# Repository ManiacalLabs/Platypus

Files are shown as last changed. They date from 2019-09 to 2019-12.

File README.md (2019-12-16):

# Platypus CNC / Laser Control Board

The Platypus is an Open Hardware CNC / Laser control board for running 2-axis GRBL with a wide variety of stepper motor driver options.

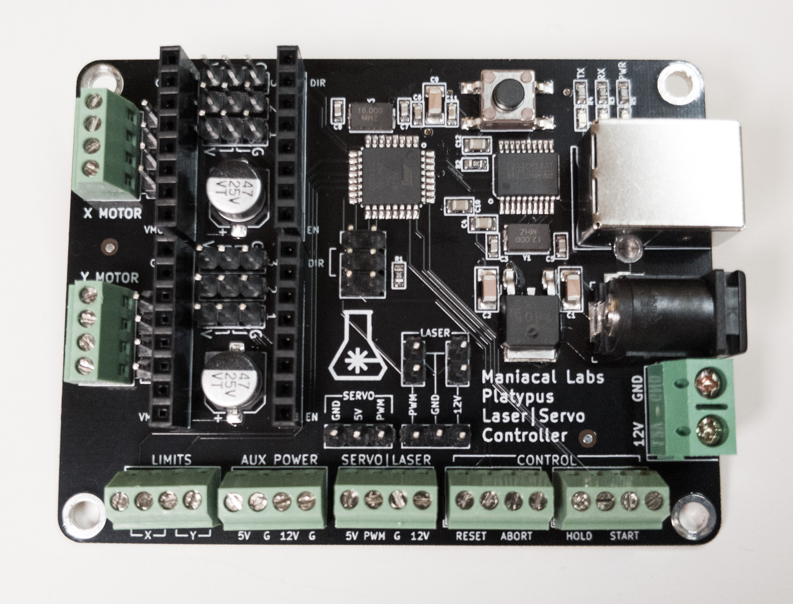
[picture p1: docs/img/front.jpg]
Platypus Controller Board


Unlike other Grbl boards that are just Arduino shields, the Platypus is a fully integrated solution with a built-in ATMega328p microcontroller and USB UART. 

Also, while other Grbl boards ignore it, the Platypus natively supports configuring Trinamic (TMC) StepStick drivers like the TMC2100 and TMC2208. Unlike normal StepStick motor drivers, the TMC variants use tri-state config pins which the Platypus provides.

# Specs

- Integrated ATMega328p Microcontroller (no arduino needed)
- CH340 USB to UART converter
- Screw terminals for all connections (plus male headers for motor and laser)
- Supports all standard StepStick-style motor drivers including TMC2100 and TMC2208
- Only 57mm x 75mm
- Robust USB-B connector

# Important Links

- [Usage](docs/Usage.md)
- [Assembly](docs/Assembly.md)

# Dimensions

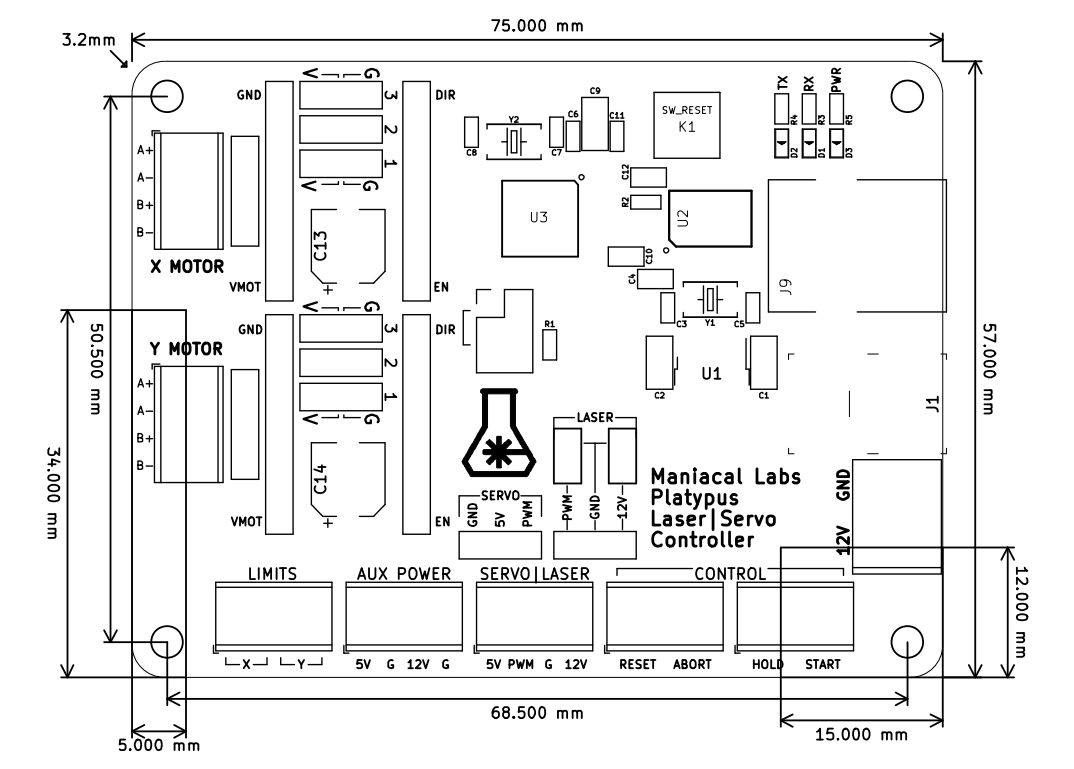
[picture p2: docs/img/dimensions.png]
Dimensions


# Contributing

This repository makes use of `git` submodules (primarily to handle KiCAD symbol and footprint libraries) and must be cloned with extra options.

Either clone the repo via:

```
git clone --recurse-submodules git@github.com:ManiacalLabs/Platypus.git
```

Or, if you already have the repo cloned or are using a fork:

```
git clone <EngravinatorRepo>
cd Engravinator
git submodule init
git submodule update
```

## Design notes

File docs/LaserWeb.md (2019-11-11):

# LaserWeb Software Setup

For using the Platypus with [LaserWeb](https://github.com/LaserWeb/LaserWeb4/) we recommend starting with the official [LaserWeb Machine Profile](https://github.com/LaserWeb/LaserWeb4/wiki/3-Settings-Machine-Profile) documentation.

Open LaserWeb and go to the `Settings` tab, where you can create a new machine profile. Select `Generic GRBL machine` from the drop-down and then click `Apply` to load that base profile.

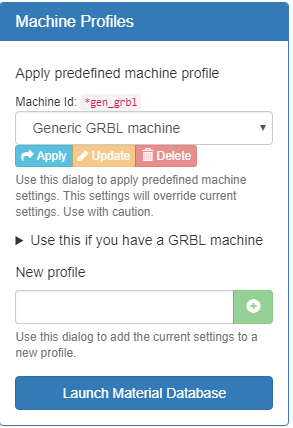
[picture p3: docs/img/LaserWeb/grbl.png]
New machine profile


Now, under the `Machine` section, enter your machine width and height (130x130mm if using the Engravinator). 

If using the Engravinator, in the `Machine Bottom Y` you must enter `-130`. There is a bug in the current UI so it sadly cannot be seen in the screenshot. This offset will be explained below.

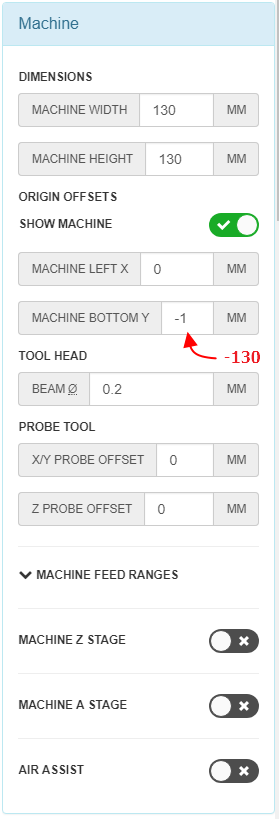
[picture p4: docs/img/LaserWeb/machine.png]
Machine section


The `File Settings` and `GCode` sections require no changes.

Under the `Application` section ensure that your machine height and width are the same values used in the `Machine` section. All other settings should be as shown, especially for the Engravinator.

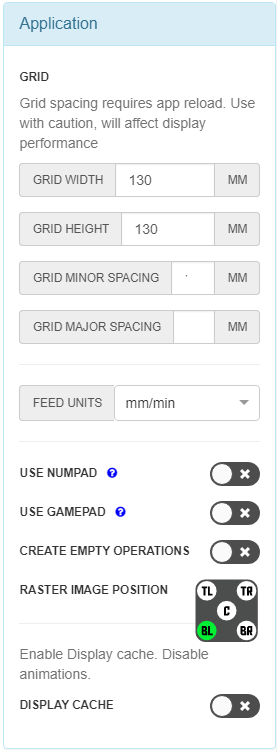
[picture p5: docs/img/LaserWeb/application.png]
Application section


For the Engravinator, you need to set a workspace offset because it does not home to the origin. In the LaserWeb console, enter `G10 L2 P1 X0 Y-130` and press enter. The Platypus comes with this offset preset but it doesn't hurt to enter it again, in case the setting was wiped. It will retain even after a power cycle. This tells the controller that the location it homed to is actually `0,130` instead of `0,0`.

Your workspace should now look as below:

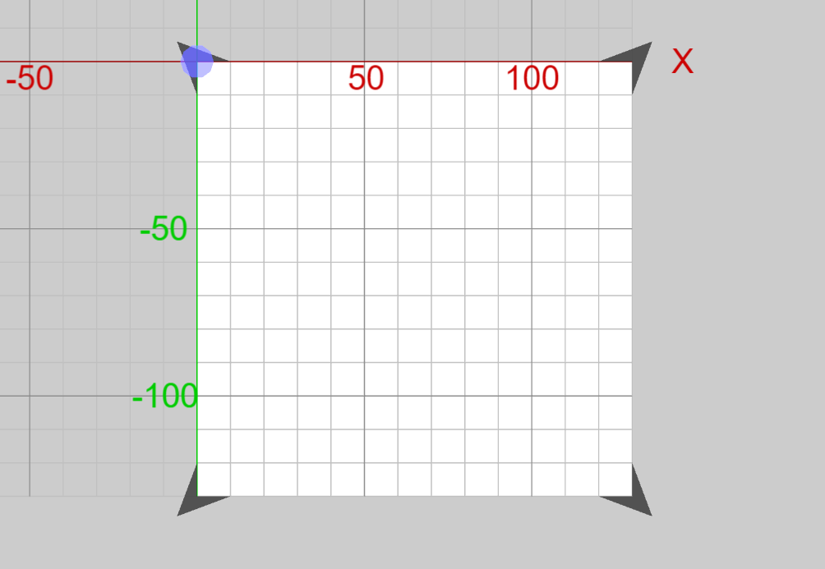
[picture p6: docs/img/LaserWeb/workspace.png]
workspace view


For the Engravinator note that the laser position is marked in the rear-left (or top-left if you prefer). As this is where it homes to, this will be the position seen after homing.

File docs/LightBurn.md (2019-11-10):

# LightBurn Software Setup

For using the Platypus with [LightBurn](https://lightburnsoftware.com) we recommend starting with the official [LightBurn New Device](https://github.com/LightBurnSoftware/Documentation/blob/master/DeviceWizard.md) documentation.

But you can also use the following for a basic setup. Click on the `Devices` button in the `Laser` window.

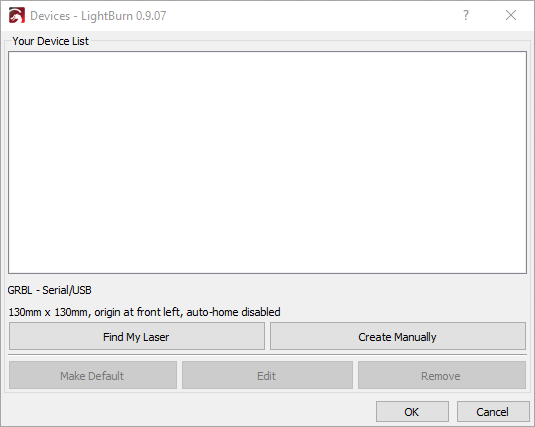
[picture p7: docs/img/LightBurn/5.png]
Devices


Either use `Find My Laser` to automatically detect and add the Platypus or click on `Create Manually`.

If using the manual setup, ensure that you select `GRBL` for the device type dialog:

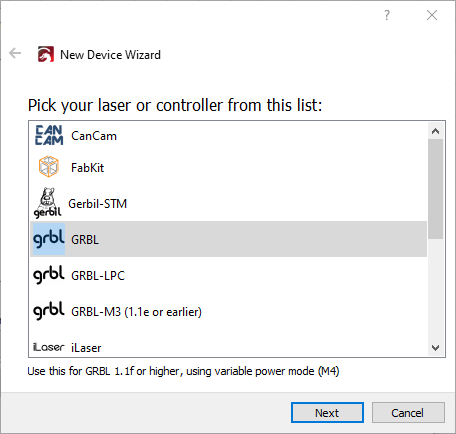
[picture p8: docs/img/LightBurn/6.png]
Device Type


Give the device a name and set your X and Y axis length. In the case of the [Engravinator](https://engravinator.com) both axis should be 130mm.

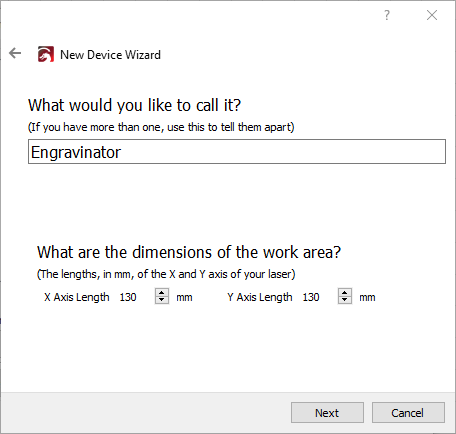
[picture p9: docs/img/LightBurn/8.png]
Name and Size


Set your origin and auto-homing. In the case of the [Engravinator](https://engravinator.com) the origin is **Front Left** even though it homes to **Rear Left**.

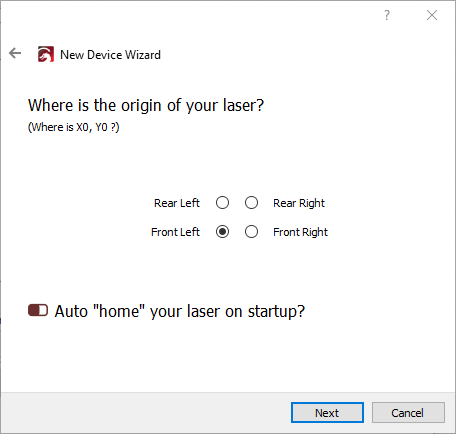
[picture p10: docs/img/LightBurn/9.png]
Origin and Homing


You should now see it connect to the Platypus in the `Console` tab. If it does not, you may need to select the serial port in the drop-down under the `Laser` tab.

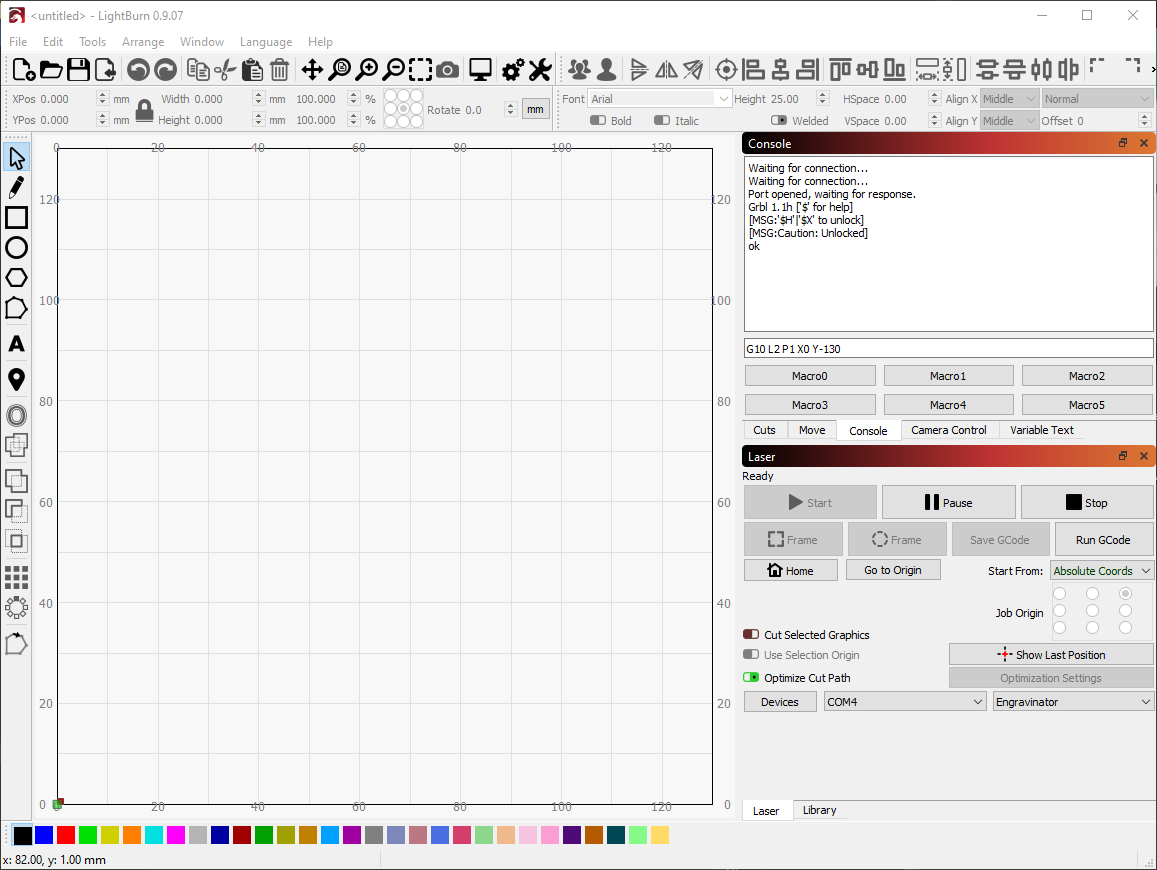
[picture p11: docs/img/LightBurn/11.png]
Connection


Please note that with the [Engravinator](https://engravinator.com) you may need to tell it that the homing location is offset from the origin. In the console, simply enter `G10 L2 P1 X0 Y-130` and press enter. The Platypus comes with this offset preset but it doesn't hurt to enter it again, in case the setting was wiped. It will retain even after a power cycle. This tells the controller that the location it homed to is actually `0,130` instead of `0,0`.

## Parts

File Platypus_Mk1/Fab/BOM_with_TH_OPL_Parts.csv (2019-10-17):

Part/Designator | Manufacture Part Number/Seeed SKU | Quantity
R3,R4,R5 | 301010298 | 3
R1,R2 | 301010299 | 2
C6,C11 | 302010139 | 2
C3,C5,C7,C8 | 302010143 | 4
C4,C10,C12 | 302010165 | 3
C1,C2,C9 | 302010181 | 3
C13,C14 | 302030059 | 2
D1,D2,D3 | 304090042 | 3
Y1 | 306010047 | 1
Y2 | 306010054 | 1
U3 | 310010049 | 1
U2 | 310070026 | 1
K1 | 311020004 | 1
J4,J5 | 320020016 | 2
J12,J14 | 320020017 | 2
J10 | 320020077 | 1
CN1,CN2,CN3,CN4,CN7,CN8,CN9,CN12 | 320020079 | 8
CN5,CN6,CN10,CN11 | 320030061 | 4
J15 | 320110031 | 1
J2,J3,J6,J7,J8,J11,J13 | 320110118 - GS019 4 pin screw terminal | 7
U1 | CJ7805(TO-252-2) 3% | 1

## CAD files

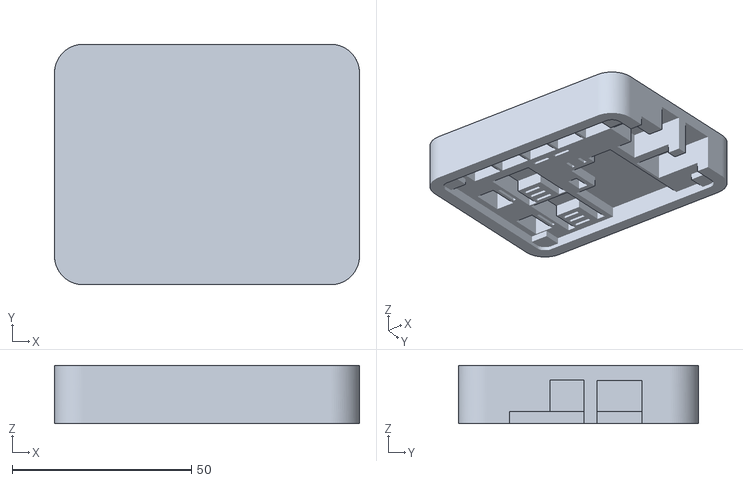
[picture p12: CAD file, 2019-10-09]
Platypus_Mk1/SolderJig.stl
85.0 x 67.0 x 16.2

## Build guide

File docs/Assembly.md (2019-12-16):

# Platypus Assembly

**If you purchased one of the pre-assembled units, you can just skip this guide!**

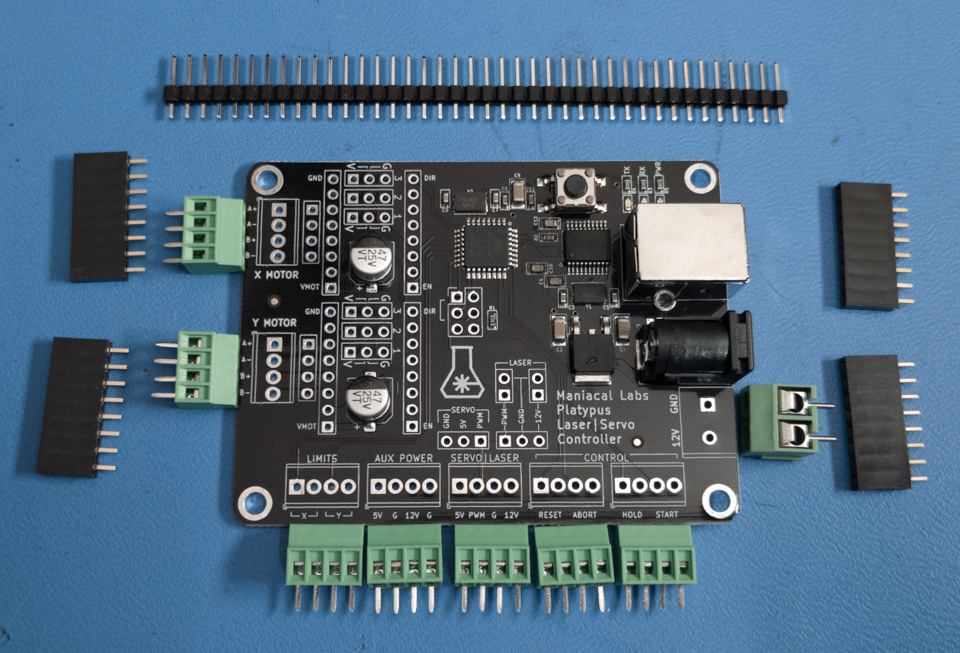
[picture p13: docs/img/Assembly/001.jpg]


Welcome to the wonderful world of the Platypus 2-Axis Laser/Servo controller! We'll be walking you through the assembly of the through-hole components which should only take 10-20 minutes.

First step is to ensure you have all the components shown above. You should have:

- Platypus main PCB
- 7x 4-pin 0.1" screw terminals
- 1x 2-pin 0.2" screw terminal
- 4x 8-pin female header
- 1x 40-pin cuttable male header

Please note that the USB port and power input barrel jack will come pre-assembled (we use these for programming).

Let's get going. We're going to do all components of each type before moving on from shortest to tallest. This allows flipping the board and having those components pushed up against the PCB.

**Note:** *Basically all of these components, except the motor driver headers, are optional depending on what you need. Check out the [Usage](Usage.md) doc and, if you decide you don't need a particular component, feel free to just leave it out.*

## Male Headers

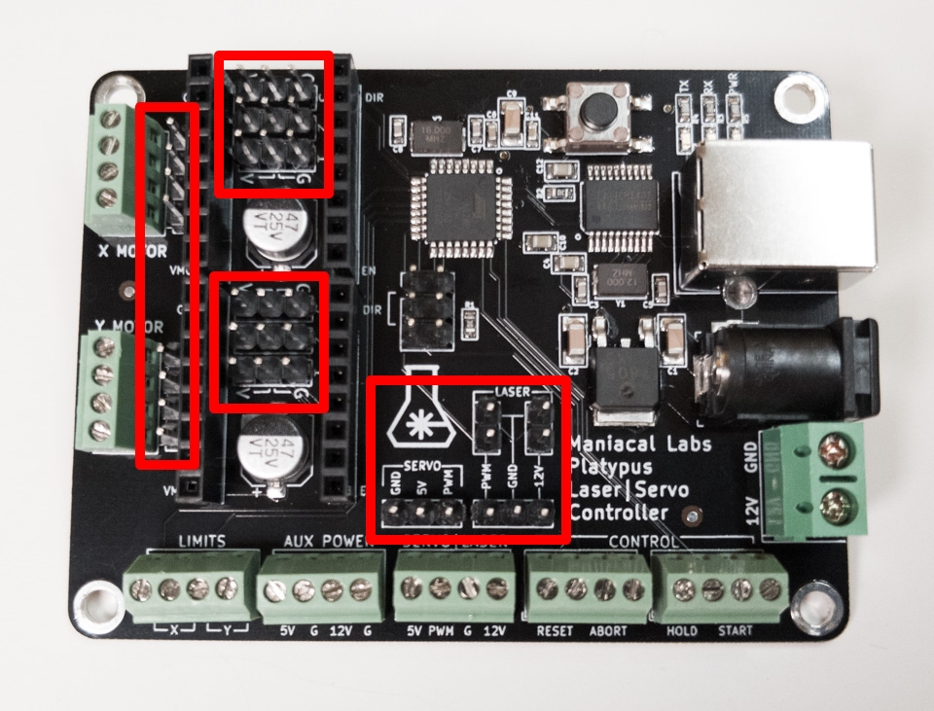
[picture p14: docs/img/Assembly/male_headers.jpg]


**Note:** *The 2x3 pin male header in the middle of the board is not included and will remain unpopulated. This is an ICSP header for programming.*

Use some flush-cut wire snips to break the 40-pin male header into the following sizes:

- 2x 4-pin
- 8x 3-pin
- 2x 2-pin

You will have one 4-pin section left. That's just spare.

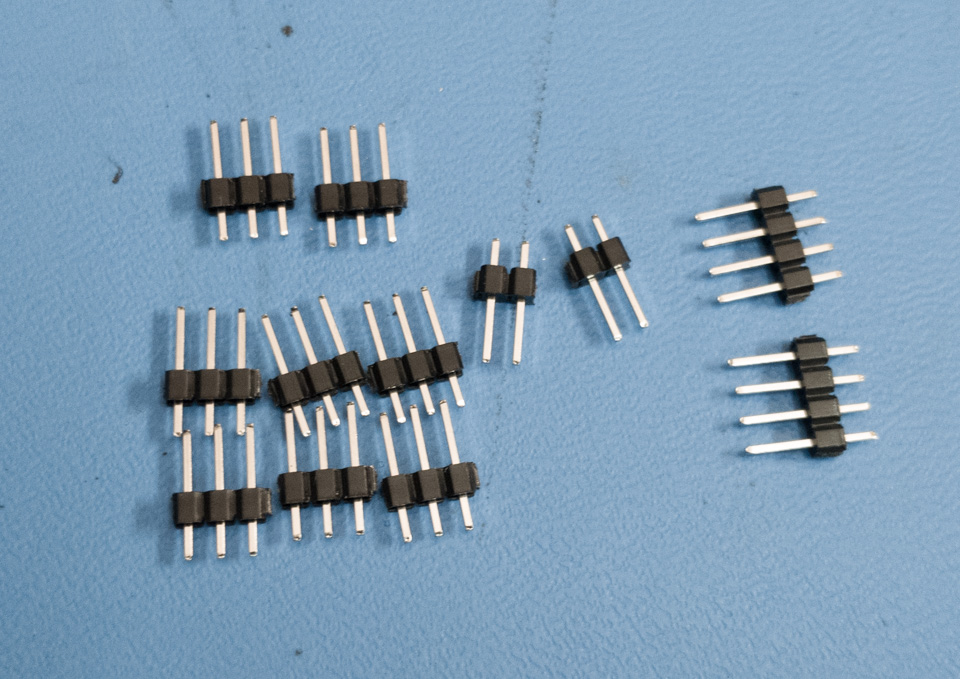
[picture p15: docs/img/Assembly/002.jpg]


For each of the male header sections, insert them into the appropriately sized spot and use some tape to hold them in place, then flip the board.

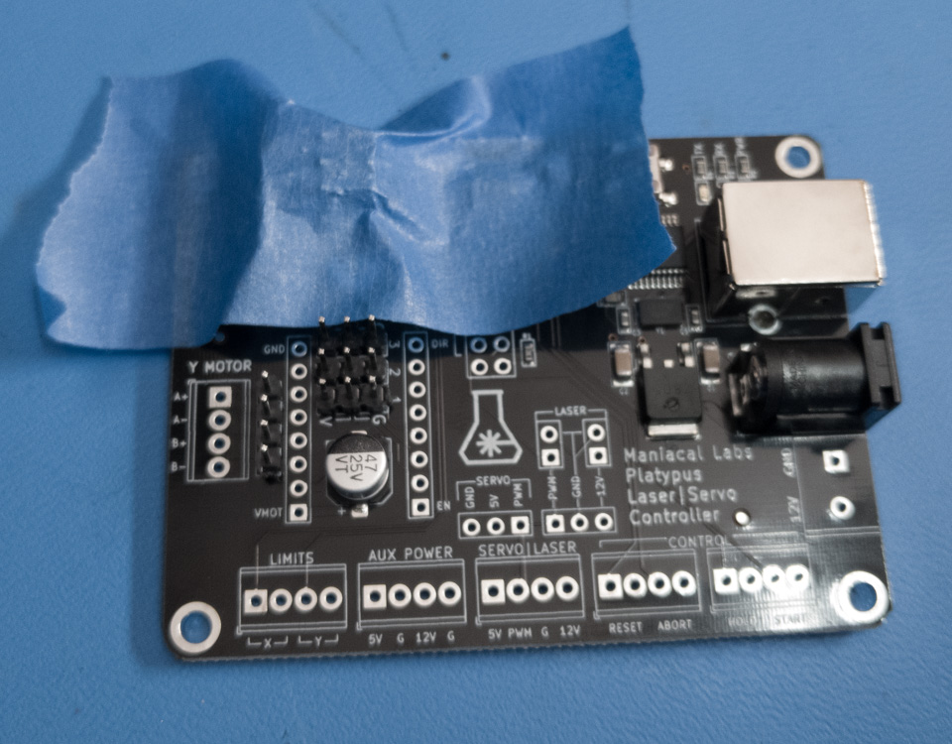
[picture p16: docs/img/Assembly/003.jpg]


**IMPORTANT** *Only solder one pin from each header section at this point!* As shown below.

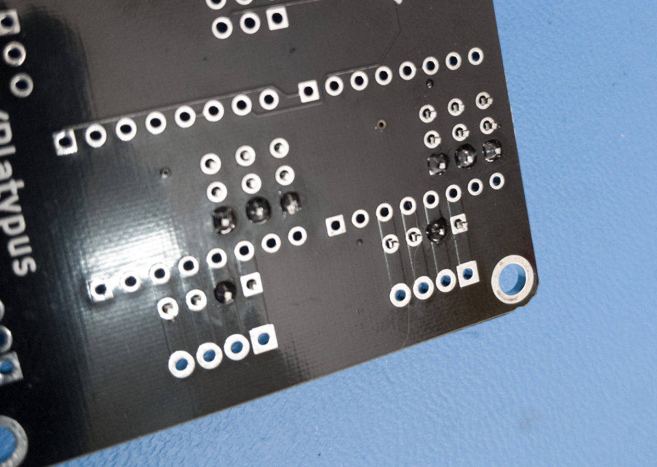
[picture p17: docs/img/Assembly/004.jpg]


Flip the board and remove the tape. If the header does not lie flush and perpendicular to the board, press on one of the pins you **DID NOT** solder with a finger and flip the board back over. Apply heat to the pin you did solder and use your finger to realign the header while the solder is molten.

Once you are happy with all the male headers, flip the board and solder all remaining pins.

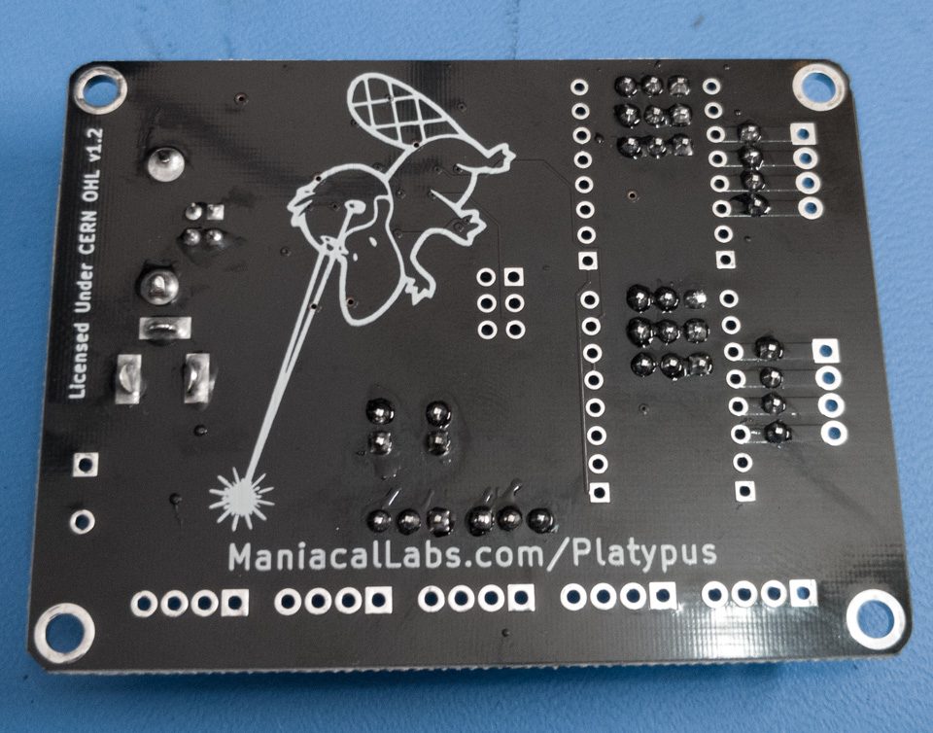
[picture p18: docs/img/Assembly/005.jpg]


## Female Motor Driver Headers

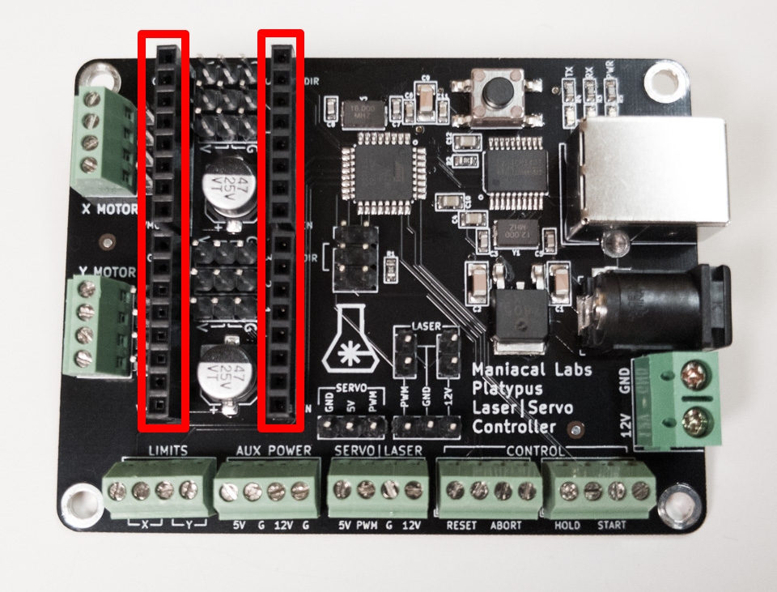
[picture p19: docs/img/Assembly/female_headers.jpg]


For this part it is important that the four 8-pin female headers be aligned correctly. We highly recommend using the (already soldered) motor drivers you plan to use to do this. 

Attach the female headers to the male headers on the motor drivers and then insert the female header pins into the front of the Platypus PCB.

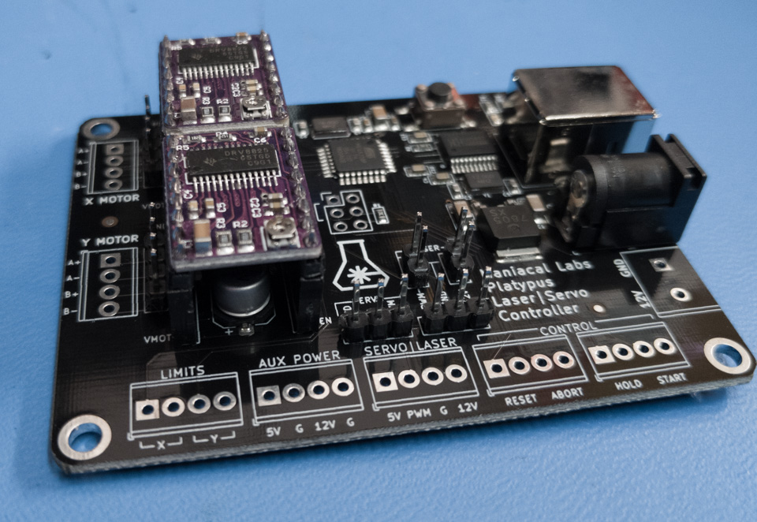
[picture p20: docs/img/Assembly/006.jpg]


Flip the board and solder only 2 pins from each motor driver, on opposing corners, as shown below.

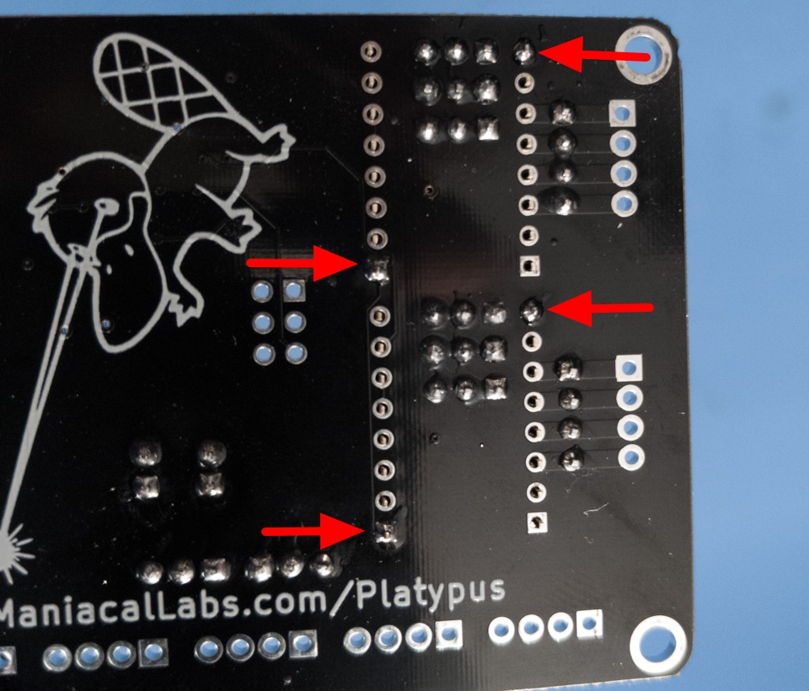
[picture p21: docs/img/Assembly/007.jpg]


Now flip the board back over and ensure that the female headers are sitting flush and perpendicular. If not, heat up the solder on those single pins and adjust. Once everything looks good, flip back over and solder all remaining pins.

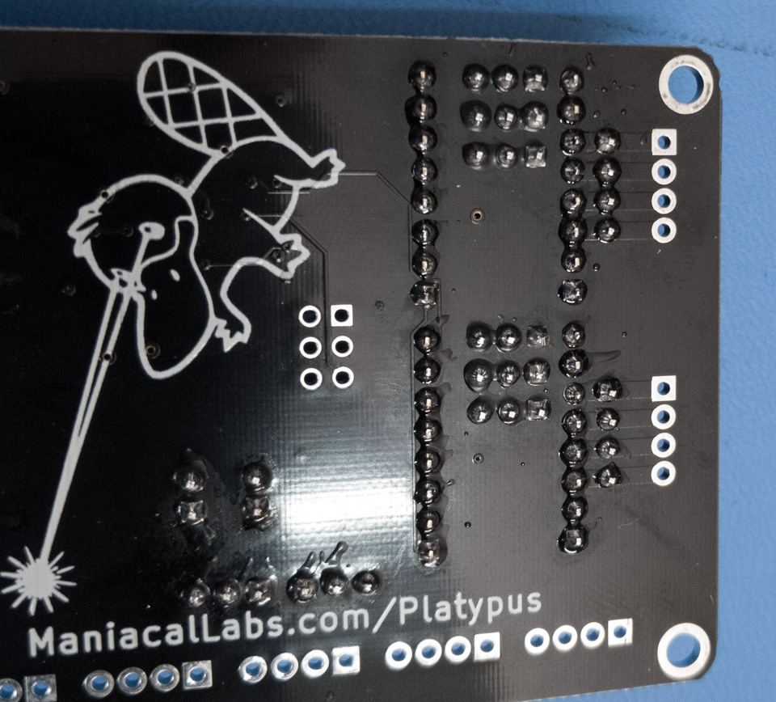
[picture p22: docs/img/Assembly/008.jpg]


## 4-pin Terminals

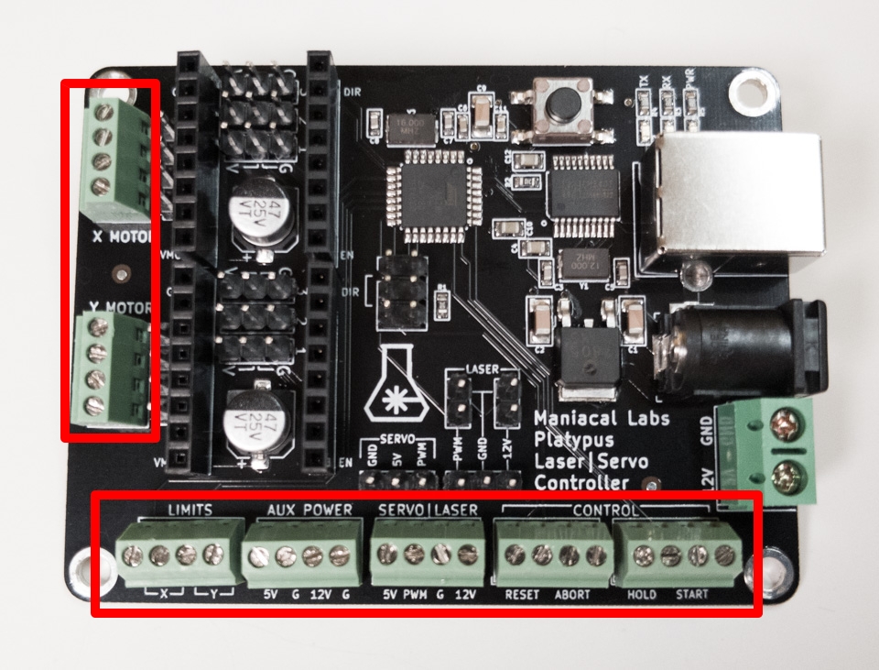
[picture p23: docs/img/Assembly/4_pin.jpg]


We recommend doing these in 2 sections: The two motor terminals and the five headers along the bottom edge. We've also found that inserting the terminals and then resting them upside-down with the top of the terminals resting on something about 20mm thick manages to keep everything nicely aligned and flush. As shown below:

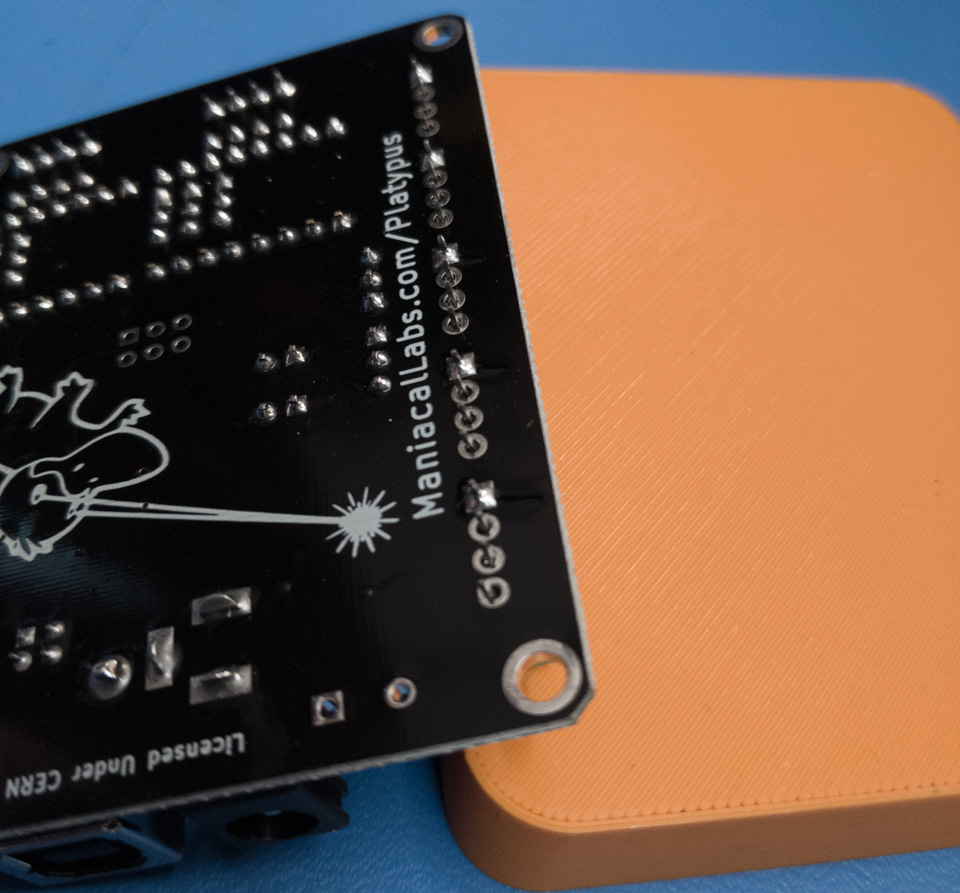
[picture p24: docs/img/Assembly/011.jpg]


**Note:** Make sure you insert the terminals with the holes for the wires facing out! As shown below:

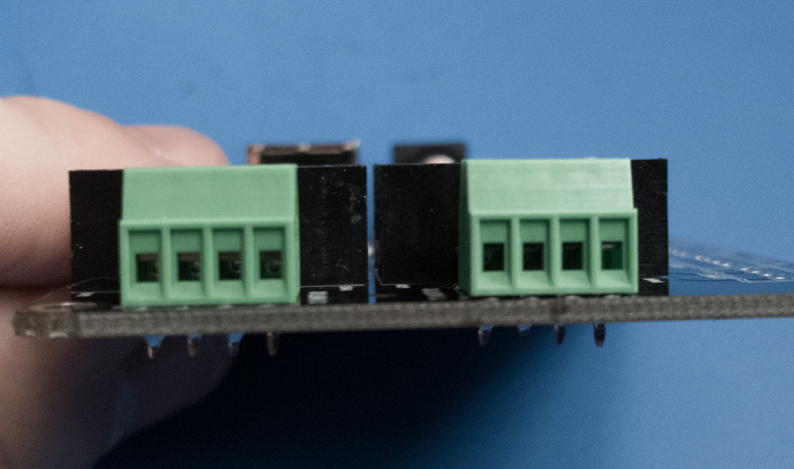
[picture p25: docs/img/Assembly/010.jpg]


Now, for each section, again you should solder just a single pin on each. Once done, flip the board and ensure that all terminals are flush and straight. 

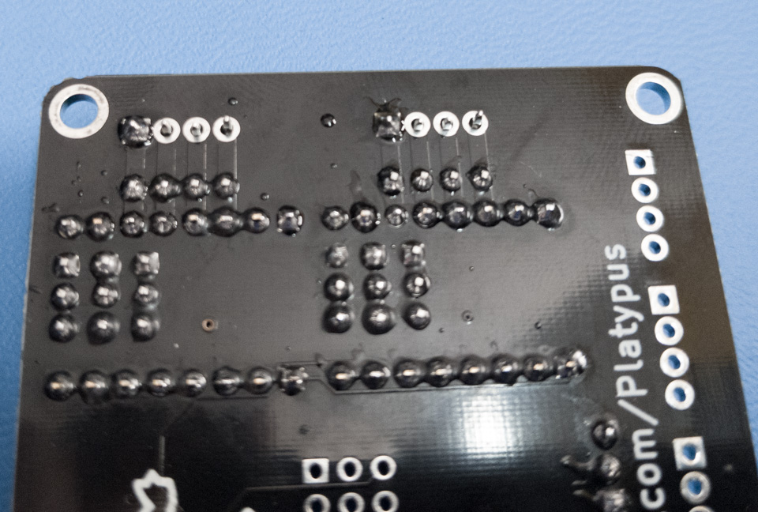
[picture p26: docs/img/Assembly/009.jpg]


Once happy with the alignment and certain that all terminals are correctly oriented, solder all remaining pins for each section.

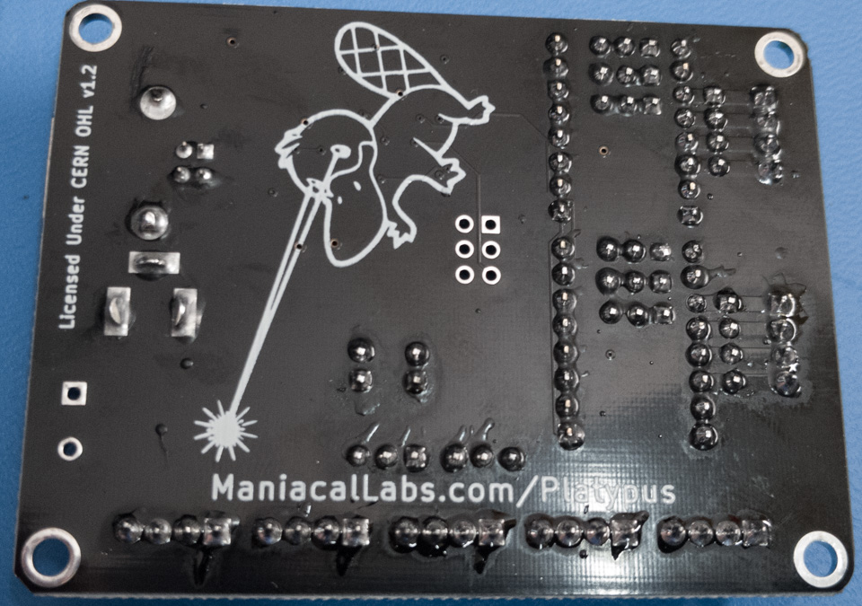
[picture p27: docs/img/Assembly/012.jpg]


## 2-pin Terminal

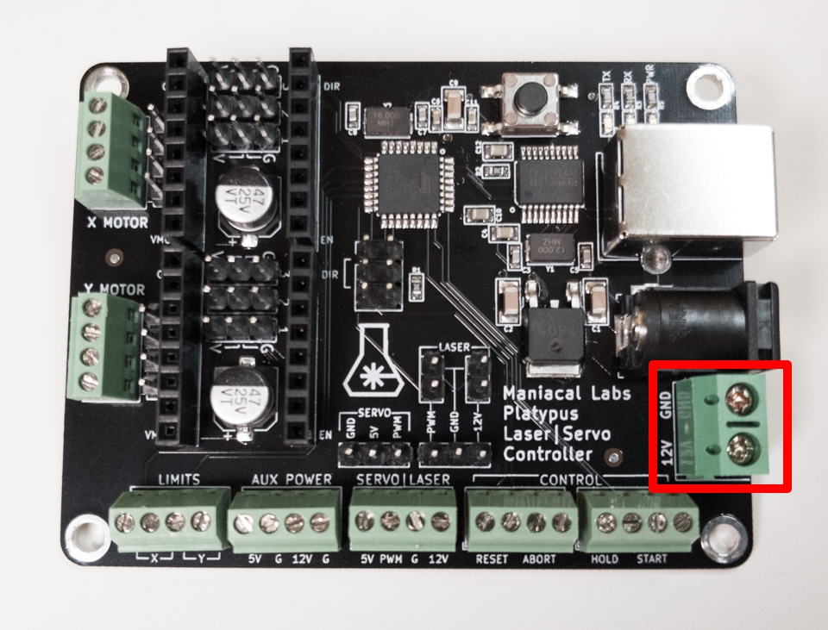
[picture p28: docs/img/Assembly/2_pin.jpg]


One more and then you are done! Though, honestly, this is the most optional of them all as you will likely be using a barrel jack power supply.

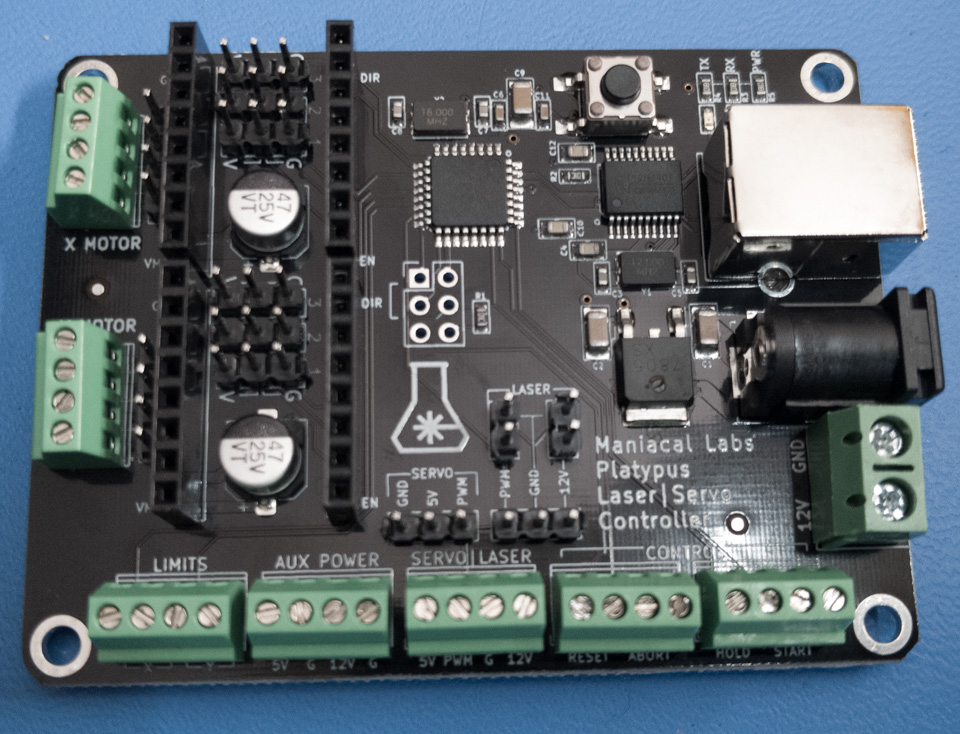
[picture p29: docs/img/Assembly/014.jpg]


This one is easy. Insert the 2-pin header, flip the board and solder. Make sure that the terminal is facing outward.

## All Done!

That's it! Head on over to the [Usage](Usage.md) guide for details on setup and usage.

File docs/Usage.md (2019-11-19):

# Platypus Controller Usage

The Platypus is designed to run standard [Grbl](https://github.com/gnea/grbl/wiki) firmware and, therefore, basically everything on the [Grbl Wiki](https://github.com/gnea/grbl/wiki) applies. The primary difference is that most Grbl hardware is a shield for an Arduino board, while the Platypus is a single, integrated, design with everything you need.

The documentation found here mainly exists to call out those things that are specific to the Platypus. Anything else can be found at the [Grbl Wiki](https://github.com/gnea/grbl/wiki).

## Software

As the Platypus uses standard Grbl you may control it with any software that supports Grbl. A lot of grbl software is pretty basic will just connect to the serial port and leave it up to you to not do anything dumb. For software with a bit more intelligence you may need some custom setup. We highly recommend checking the documentation for that software but for those below we've created some simple quick-start guides:

- [LightBurn](LightBurn.md)
- [LaserWeb](LaserWeb.md)

## Drivers

On most modern operating systems will recognize the CH340 USB to UART adapter and load the drivers automatically and there's noting you need to do.

If, for some reason, your system doesn't automatically recognize the device and you need to install drivers, SparkFun already has a fantastic primer on the CH340 chip and how to get it up and running:

[How to Install CH340 Drivers](https://learn.sparkfun.com/tutorials/how-to-install-ch340-drivers/)

## Connections

All necessary connections are clearly labeled on the PCB itself as seen below. Note that for `LIMITS` and `CONTROL` headers there is no polarity requirement as they are expected to be used with "Normally Open" switches.

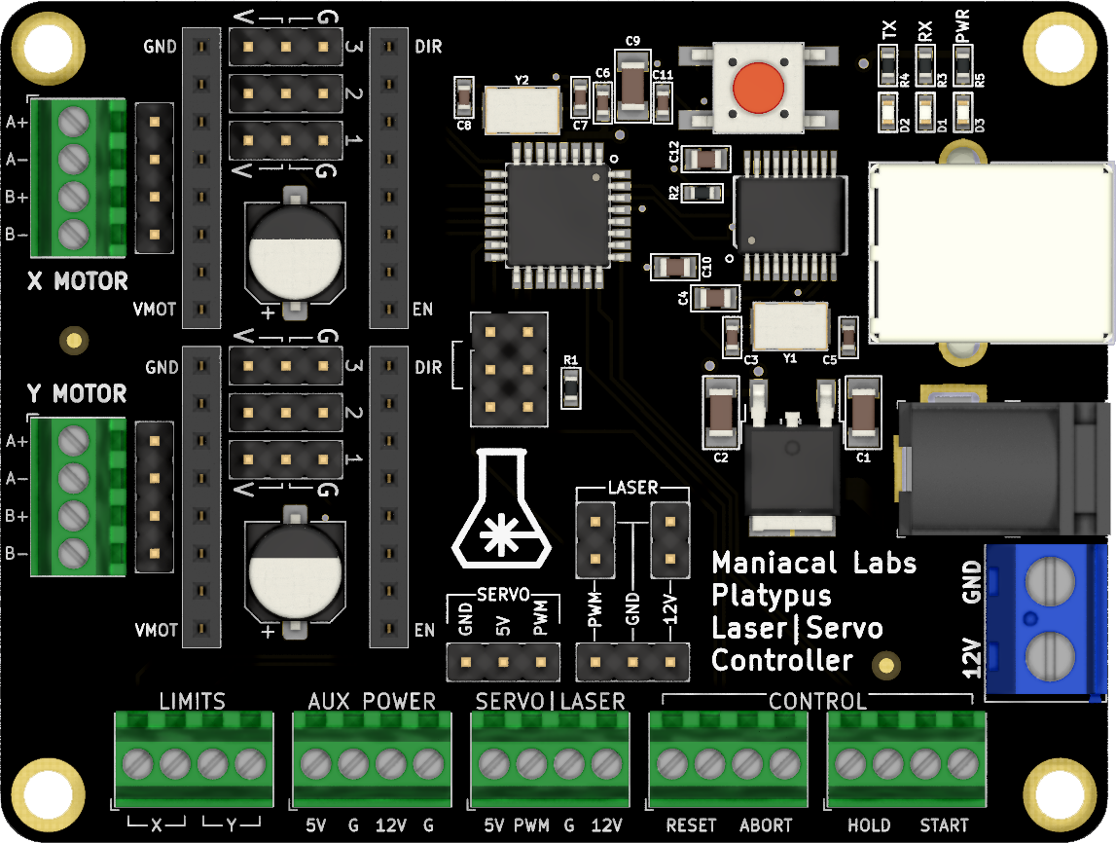
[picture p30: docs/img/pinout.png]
Platypus Pinout


### Power

You may either use the 2.1mm, center-positive barrel connector or the large screw terminal for the required input power. 

Please note that the Platypus was designed specifically as a 12V system. DO NOT connect any power other than 12V!

It is recommended to use a power supply that can provide at least 5A.

Finally, note that the Platypus **must** have the 12V supply connected to power up the microcontroller. The USB input **will not** provide any power.

### Motors

You may use either the screw terminals or male headers, depending on the wiring available on your motors. Simply follow the motor phase labels as defined by your motor datasheet. Typically the wires are connected in Blue, Red, Green, Black order. If your motor is running in the wrong direction you can either swap the wire order 180&deg; or [flip the direction mask in Grbl](https://github.com/gnea/grbl/wiki/Grbl-v1.1-Configuration#3--direction-port-invert-mask).

### Laser

If you are using a diode laser it likely came with a cable that is 3-pin on the diode side and either 3-pin or 2x 2-pin on the controller side.

If it uses 3-pin on the controller side, simply connect it to the 3-pin laser male header. Note that, for most lasers:

- Red -> 12V
- Black -> Ground
- Yellow -> PWD

If it uses a 2x 2-pin controller (as in 2 separate 2-pin female connectors), then use the dual 2-pin male headers directly above the 3-pin header. Note that the top-most pins are ground. The same color coding as above applies.

Finally, you can also use the screw terminal. Strip ~3mm of insulation off the end of each wire and connect to `PWM`, `G`, and `12V` on the `SERVO|LASER` terminal. If your have 2 ground wires, just connect both to the `G` terminal. The `5V` connection is not needed as most lasers are 12V.

### Servo

**Note:** Remember that you will need to use different firmware for servo control.

Typically, your servo will come with a 3-pin female connector. In that case, just use the 3-pin male header labeled `SERVO`.

- Brown -> GND
- Red -> 5V
- Orange -> PWM

You may also use the `SERVO|LASER` screw terminal, using the above labeled color mapping. Simply remove ~3mm of insulation from each wire and connect to the screw terminal.

## Limits

For more detailed information see the official Grbl [Wiring Limit Switches](https://github.com/gnea/grbl/wiki/Wiring-Limit-Switches) documentation.

As it's the easiest setup, we recommend using "Normally Open" switches as no firmware changes will be required. If using 2 switches per axis, you may then simply wire both to the same input in parallel. Again, see above linked Grbl documentation for more details.

### Control

As noted, none of these connections require specific polarity. Just use a "Normally Open" switch.

- **RESET**: Connected directly to the microcontroller **Reset** pin. This will immediately reboot the controller and stop all motion.
- **ABORT**: Force Grbl into an ALARM state. **Not** guaranteed to stop immediately. Recommend using above **RESET** pin instead.
- **HOLD**: Pause all motion. Can be resumed with the **START** command or pin.
- **START**: Resume after a hold.

## Motor Drivers

The Platypus supports all standard "StepStick" style motor drivers, such as A4988, DRV8825, TMC2100, and TMC2208. Unlike most other Grbl controllers available, however, the Platypus actually supports jumper configuration of Trinamic (TMC) drivers as it provides both high and low jumpers.

Be sure to align your motor driver pins with the labeled `GND`, `DIR` (direction), `EN` (enable), and `VMOT` (motor voltage). It is important to note that TMC drivers will be inserted with the IC facing down, towards the controller.

To save you the trouble of tracking down how to configure each different driver, we've provided config tables and Vref (for current limiting) formulas below. Note that `O` means `Open` so no jumper is needed. Please see the specific motor driver's documentation on more specific information on configuration and how to set the current limiting.

### A4988

| CFG1 | CFG2 | CFG3 | MicroSteps | 
|---|---|---|---|
| O | O | O | 1/1 | 
| V | O | O | 1/2 | 
| O | V | O | 1/4 | 
| V | V | O | 1/8 | 
| V | V | V | 1/16 | 

Vref = 8 * Imax * 0.068

### DRV8825

| CFG1 | CFG2 | CFG3 | MicroSteps | 
|---|---|---|---|
| O | O | O | 1/1 | 
| V | O | O | 1/2 | 
| O | V | O | 1/4 | 
| V | V | O | 1/8 | 
| O | O | V | 1/16 | 
| V | V | V | 1/32 | 

Vref = Imax / 2

### TMC2100

| CFG1 | CFG2 | CFG3 | MicroSteps | Notes | 
|---|---|---|---|---|
| G | G | O | 1/1 | SpreadCycle / No Interp  | 
| V | G | O | 1/2 | SpreadCycle / No Interp  | 
| O | G | O | 1/2 | SpreadCycle / 256 Interp | 
| G | V | O | 1/4 | SpreadCycle / No Interp  | 
| V | V | O | 1/16 | SpreadCycle / No Interp  | 
| O | V | O | 1/4 | SpreadCycle / 256 Interp | 
| G | O | O | 1/16 | SpreadCycle / 256 Interp | 
| V | O | O | 1/4 | StealthChop / 256 Interp | 
| O | O | O | 1/16 | StealthChop / 256 Interp | 

Vref = Imax

### TMC2208

| CFG1 | CFG2 | CFG3 | MicroSteps | Notes | 
|---|---|---|---|---|
| V | G | O | 1/2 | StealthChop2 / 256 Interp | 
| G | V | O | 1/4 | StealthChop2 / 256 Interp | 
| G | G | O | 1/8 | StealthChop2 / 256 Interp | 
| V | V | O | 1/16 | StealthChop2 / 256 Interp | 

Vref = Imax

The TMC2208 also supports SpreadCycle but that must be configured over UART manualy.

## Firmware

The Platypus comes with basic 2-axis Grbl firmware pre-installed. This is important as the default Grbl assumes you will be using 3 axis and homing will fail because there's no Z axis to home in this case. Unfortunately fixing this requires modifying `config.h` in Grbl. Fortunately, we've done the hard work for you.

Note that it also comes pre-configured with all the Grbl settings required for the [Engravinator](https://engravinator.com). If you need to change these settings, please see the official [Grbl Configuration](https://github.com/gnea/grbl/wiki/Grbl-v1.1-Configuration) documentation.

You should not generally need to ever upload new firmware, but if you do we recommend starting with the [official Platypus config.h](https://github.com/ManiacalLabs/grbl/blob/master/configs/2_axis/config.h) as a jumping-off point.

You may also download the [default firmware hex](https://github.com/ManiacalLabs/grbl/blob/builds/2_axis.hex) and upload it to your board via avrdude or XLoader.

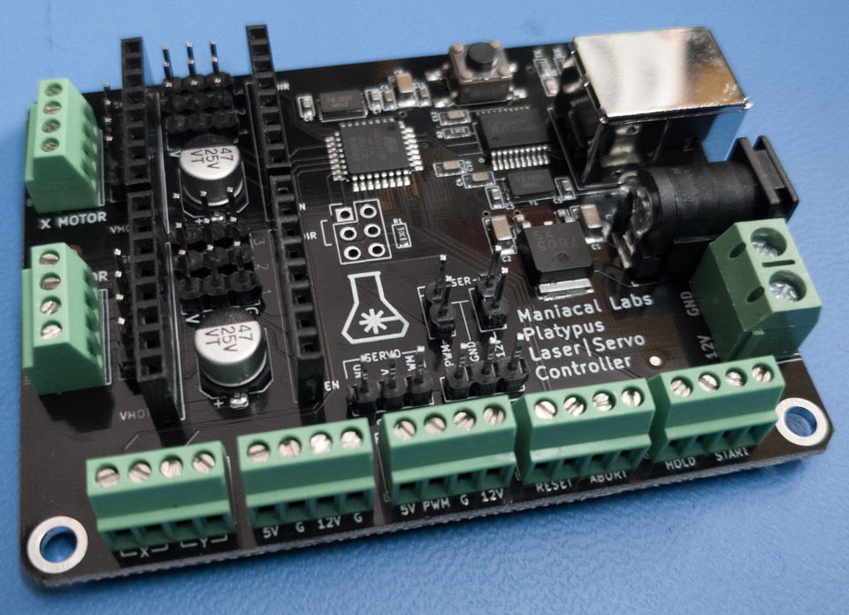
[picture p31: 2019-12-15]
docs/img/Assembly/013.jpg

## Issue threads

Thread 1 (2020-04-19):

Signal Pin for Servo

jstoddart, 2020-04-19:
What is the pin assignment for the servo PWM signal pin? (A pinout diagram would be great for general documentation purposes).

I'm working on a grbl variant with servo control with the assumption it was pin 11, but I can't tell if I have the wrong pin assigned or a burned out servo.

jstoddart, 2020-04-19:
Apologies -- found another servo and confirmed it was a dead servo issue. Pinout would still be good for documentation, in case someone wants to develop / implement a GRBL alternative.

Closed 2020-04-19.

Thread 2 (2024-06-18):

What are the pins for controling stepper drivers over UART?

pjoyce42, 2024-06-18:
I realize this project is long since retired, but here goes. I'm trying to port my Platypus over to Klipper, and the config is requiring a UART pin number for the stepper drivers. Are they hooked up to the microcontroller, if so, which pins are used? I can't find them in the CPU Pin map, and probing the boards is not helping. Thanks.

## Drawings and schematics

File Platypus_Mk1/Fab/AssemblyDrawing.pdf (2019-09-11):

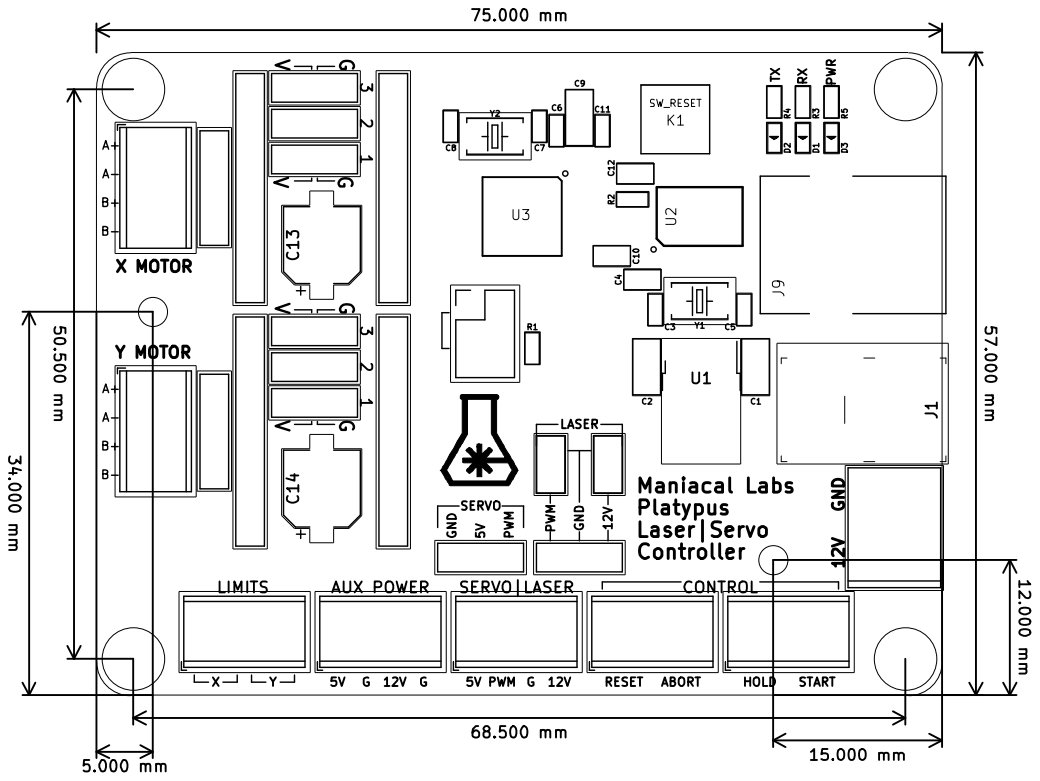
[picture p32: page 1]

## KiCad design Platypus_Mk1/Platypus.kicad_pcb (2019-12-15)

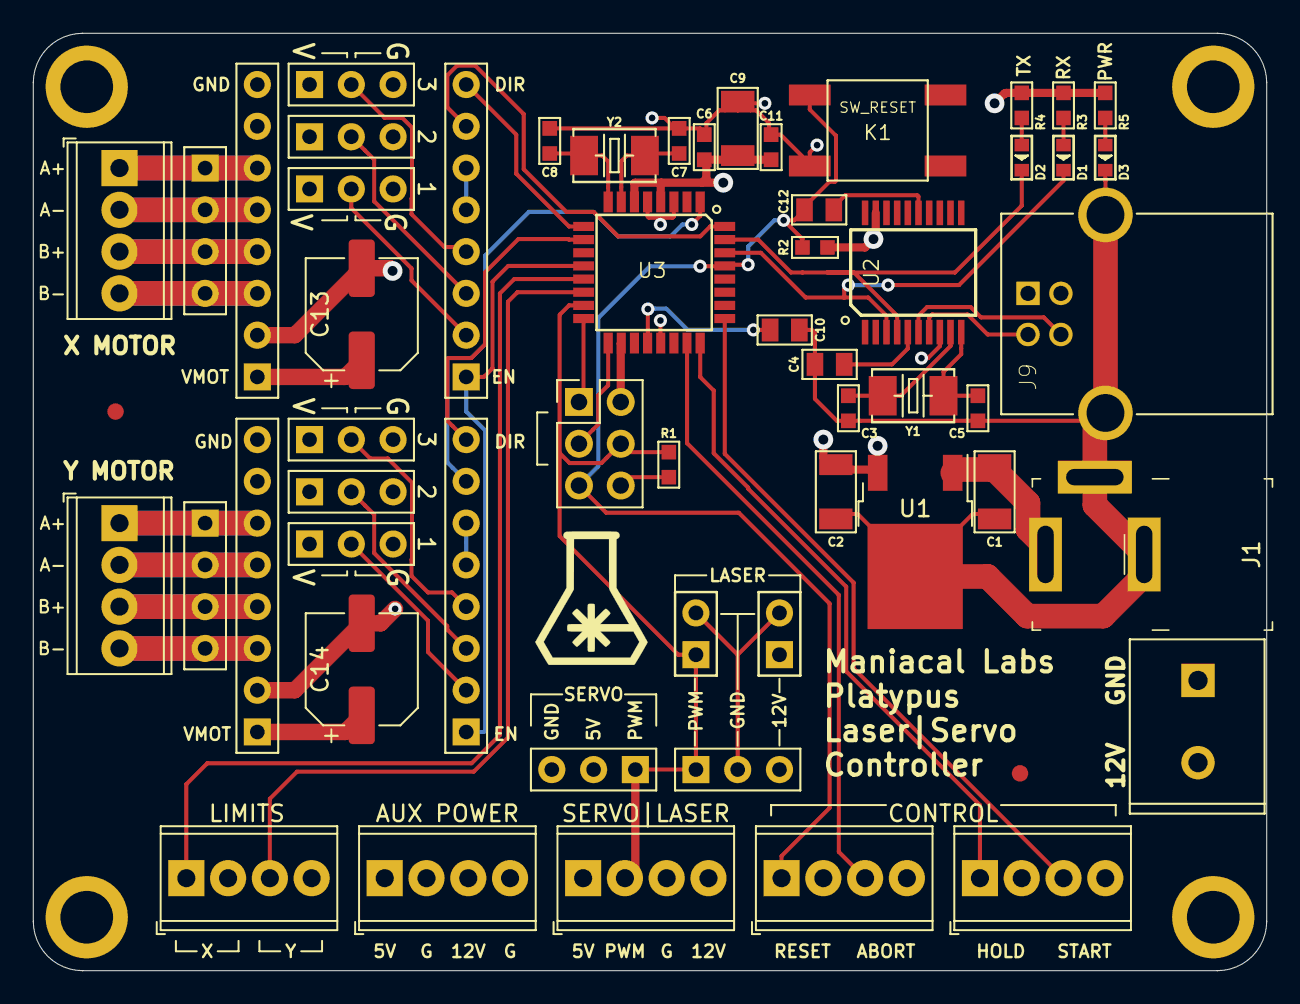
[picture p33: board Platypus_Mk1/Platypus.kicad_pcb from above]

Board: 4 copper layers, 75.0 x 57.0 mm, 61 parts (0 on the bottom side), 47 nets.

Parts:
C1, C2, C9: 10uF; C1206
C3, C5, C7, C8: 22pF; C0603
C4, C10, C12: 100nF; C0805
C6, C11: 1uF; C0603
C13, C14: 47uF; CP_Elec_6.3x5.4
CN1: SERVO_PWM; H3-2.54
CN2, CN3, CN4, CN7, CN8, CN9: CFG1; H3-2.54
CN5, CN10: FEMALE_LEFT; H8-2.54
CN6, CN11: FEMALE_RIGHT; H8-2.54
CN12: LASER_CONN; H3-2.54
D1, D2, D3: LED_RED; LED-0603
FID1, FID2: Fiducial; Fiducial_1mm_Dia_2mm_Outer
H1, H2, H3, H4: Mount; MountingHole_2.5mm_Pad
J1: PJ-202AH; Barrel_Jack_5.5mmODx2.1mmID_PJ-202A
J2: TermLaser; TerminalBlock_Phoenix_MPT-0,5-4-2.54_1x04_P2.54mm_Horizontal
J3: TermStop; TerminalBlock_Phoenix_MPT-0,5-4-2.54_1x04_P2.54mm_Horizontal
J4: LASER_PWR; H2-2.54
J5: LASER_PULSE; H2-2.54
J6: TermControl; TerminalBlock_Phoenix_MPT-0,5-4-2.54_1x04_P2.54mm_Horizontal
J7: TermLimit; TerminalBlock_Phoenix_MPT-0,5-4-2.54_1x04_P2.54mm_Horizontal
J8: TermAux; TerminalBlock_Phoenix_MPT-0,5-4-2.54_1x04_P2.54mm_Horizontal
J9: UJ2-BH-1-TH; CUI_UJ2-BH-1-TH
J10: ICSP; PinHeader_2x03_P2.54mm_Vertical
J11, J13: MotorTerm; TerminalBlock_Phoenix_MPT-0,5-4-2.54_1x04_P2.54mm_Horizontal
J12, J14: MotorHeader; H4-2.54
J15: 12V_TERM; H2-5.0-10.5X8.0MM
K1: SW_RESET; SW4-SMD-6.0X6.0X5.0MM
R1, R2: 10K; R0603
R3, R4, R5: 1K; R0603
U1: CJ7805; TO-252-2
U2: INTERFACE-CH340T_SSOP20_; SSOP20-0.65-7.6X5.2MM
U3: MCU-ATMEGA328P-AU_TQFP32_; TQFP32-0.8-7X7MM
Y1: 12MHz; X2-SMD-5.0X3.2X1.3MM
Y2: 16MHZ; X2-SMD-5.0X3.2X1.3MM

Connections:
5V: C2.1, C6.2, C9.1, C11.2, CN1.2, CN2.1, CN3.1, CN4.1, CN6.7, CN7.1, CN8.1, CN9.1, CN11.7, J2.1, J8.1, J10.2, R2.2, R3.2, R4.1, R5.2, U1.3, U2.19, U3.4, U3.6, U3.18
/Arduino Nano/D12: J10.1, U3.16
/Arduino Nano/D13: J10.3, U3.17
/GRBL_ABORT: J3.3, U3.23
/GRBL_RX: D1.2, U2.3, U3.30
/GRBL_TX: D2.2, U2.4, U3.31
/HOLD: J6.1, U3.24
/NANO_RESET: C12.1, J3.1, J10.5, K1.3, R2.1, U3.29
/PULSE: CN1.1, CN12.1, J2.2, J5.1, J10.4, R1.2, U3.15
/START: J6.3, U3.25
/STEP_EN: CN5.1, CN10.1, U3.12
/StepDriverX/CFG1: CN2.2, CN5.2
/StepDriverX/CFG2: CN3.2, CN5.3
/StepDriverX/CFG3: CN4.2, CN5.4
/StepDriverY/CFG1: CN7.2, CN10.2
/StepDriverY/CFG2: CN8.2, CN10.3
/StepDriverY/CFG3: CN9.2, CN10.4
/VIN_12V: C1.1, C13.1, C14.1, CN6.1, CN11.1, CN12.3, J1.1, J2.4, J4.1, J8.3, J15.2, U1.1
/X_DIR: CN5.8, U3.9
/X_LIMIT: J7.1, U3.13
/X_STEP: CN5.7, U3.32
/Y_DIR: CN10.8, U3.10
/Y_LIMIT: J7.3, U3.14
/Y_STEP: CN10.7, U3.1
GND: C1.2, C2.2, C3.1, C4.2, C5.1, C6.1, C7.2, C8.1, C9.2, C10.2, C11.1, C13.2, C14.2, CN1.3, CN2.3, CN3.3, CN4.3, CN6.2, CN6.8, CN7.3, CN8.3, CN9.3, CN11.2, CN11.8, CN12.2, D3.2, H1.1, H2.1, H3.1, H4.1, J1.2, J1.3, J2.3, J3.2, J3.4, J4.2, J5.2, J6.2, J6.4, J7.2, J7.4, J8.2, J8.4, J9.4, J9.SH1, J9.SH2, J10.6, J15.1, K1.4, R1.1, U1.2, U2.8, U3.3, U3.5, U3.21
unnamed: C3.2, U2.9, Y1.2
unnamed: C4.1, U2.5
unnamed: C5.2, U2.10, Y1.1
unnamed: C7.1, U3.7, Y2.1
unnamed: C8.2, U3.8, Y2.2
unnamed: C10.1, U3.20
unnamed: C12.2, U2.15
unnamed: CN5.5, CN5.6
unnamed: CN6.3, J11.4, J12.4
unnamed: CN6.4, J11.3, J12.3
unnamed: CN6.5, J11.2, J12.2
unnamed: CN6.6, J11.1, J12.1
unnamed: CN10.5, CN10.6
unnamed: CN11.3, J13.4, J14.4
unnamed: CN11.4, J13.3, J14.3
unnamed: CN11.5, J13.2, J14.2
unnamed: CN11.6, J13.1, J14.1
unnamed: D1.1, R3.1
unnamed: D2.1, R4.2
unnamed: D3.1, R5.1
unnamed: J9.2, U2.7
unnamed: J9.3, U2.6

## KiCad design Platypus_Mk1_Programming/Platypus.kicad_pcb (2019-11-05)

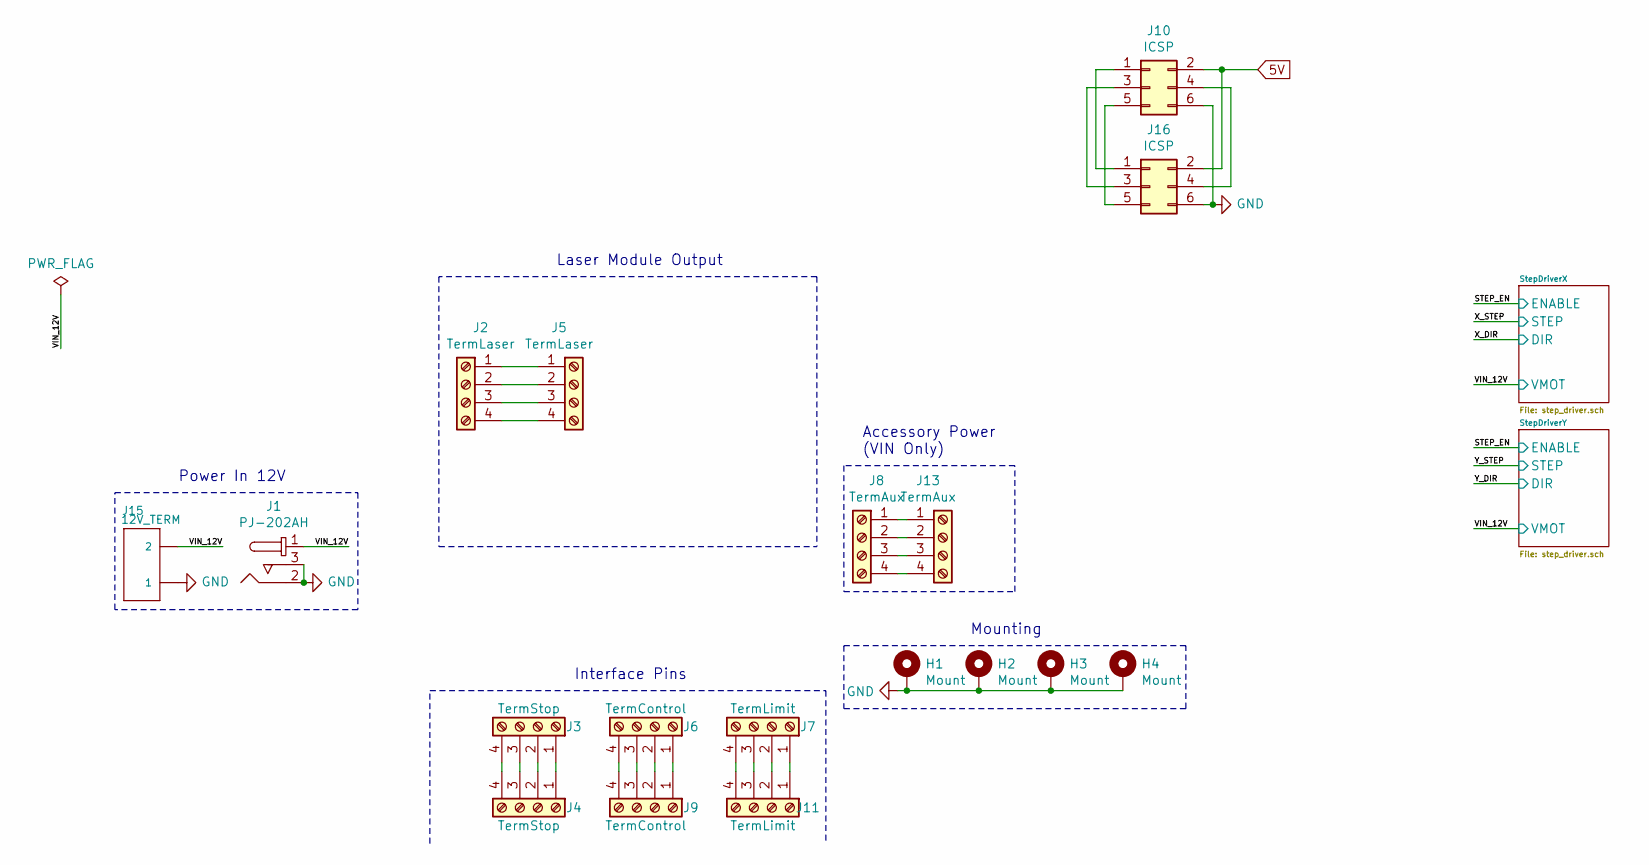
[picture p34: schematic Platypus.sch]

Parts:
H1, H2, H3, H4: Mount; MountingHole_2.5mm_Pad
J1: PJ-202AH; Barrel_Jack_5.5mmODx2.1mmID_PJ-202A; MPN PJ-202AH; Digi-Key_PN CP-202AH-ND
J2, J5: TermLaser; TerminalBlock_Phoenix_MPT-0,5-4-2.54_1x04_P2.54mm_Horizontal; MPN GS019-2.54-04P-5
J3, J4: TermStop; TerminalBlock_Phoenix_MPT-0,5-4-2.54_1x04_P2.54mm_Horizontal; MPN GS019-2.54-04P-5
J6, J9: TermControl; TerminalBlock_Phoenix_MPT-0,5-4-2.54_1x04_P2.54mm_Horizontal; MPN GS019-2.54-04P-5
J7, J11: TermLimit; TerminalBlock_Phoenix_MPT-0,5-4-2.54_1x04_P2.54mm_Horizontal; MPN GS019-2.54-04P-5
J8, J13: TermAux; TerminalBlock_Phoenix_MPT-0,5-4-2.54_1x04_P2.54mm_Horizontal; MPN GS019-2.54-04P-5
J10, J16: ICSP; PinHeader_2x03_P2.54mm_Vertical; MPN P125-12A1BS116A1
J15: 12V_TERM; H2-5.0-10.5X8.0MM

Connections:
5V: J10.2, J16.2; also elsewhere on the board
/VIN_12V: J1.1, J15.2; also elsewhere on the board
GND: H1.1, H2.1, H3.1, H4.1, J1.2, J1.3, J10.6, J15.1, J16.6; also elsewhere on the board
unnamed: J2.1, J5.1
unnamed: J2.2, J5.2
unnamed: J2.3, J5.3
unnamed: J2.4, J5.4
unnamed: J3.1, J4.1
unnamed: J3.2, J4.2
unnamed: J3.3, J4.3
unnamed: J3.4, J4.4
unnamed: J6.1, J9.1
unnamed: J6.2, J9.2
unnamed: J6.3, J9.3
unnamed: J6.4, J9.4
unnamed: J10.1, J16.1
unnamed: J10.3, J16.3
unnamed: J10.4, J16.4
unnamed: J10.5, J16.5
unnamed: J7.1, J11.1
unnamed: J7.2, J11.2
unnamed: J7.3, J11.3
unnamed: J7.4, J11.4
unnamed: J8.1, J13.1
unnamed: J8.2, J13.2
unnamed: J8.3, J13.3
unnamed: J8.4, J13.4

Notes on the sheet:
Accessory Power (VIN Only)
Laser Module Output
Interface Pins
Power In 12V
Mounting

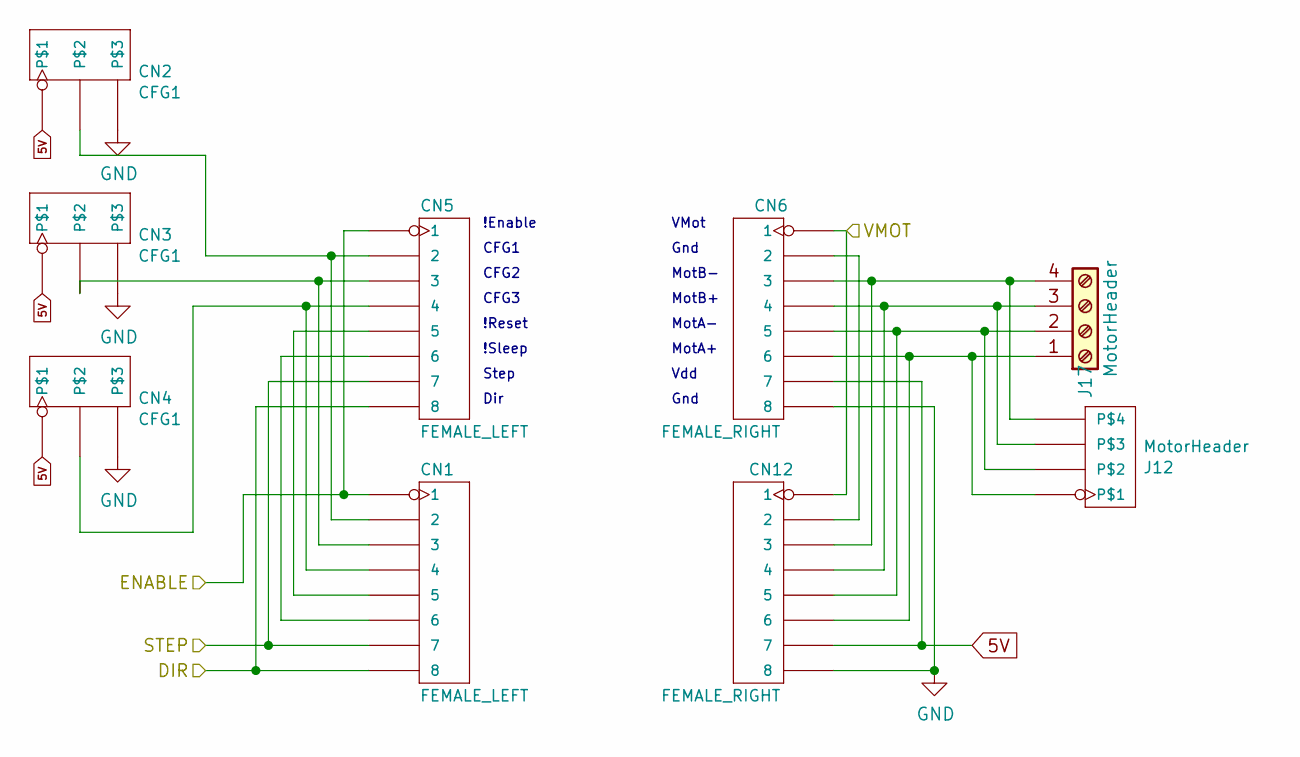
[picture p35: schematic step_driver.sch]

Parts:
CN1, CN5: FEMALE_LEFT; H8-2.54; MPN F185-1108A1BSYC1
CN2, CN3, CN4: CFG1; H3-2.54
CN6, CN12: FEMALE_RIGHT; H8-2.54; MPN F185-1108A1BSYC1
J12: MotorHeader; H4-2.54; MPN P125-1104A0BS116A1
J17: MotorHeader; TerminalBlock_Phoenix_MPT-0,5-4-2.54_1x04_P2.54mm_Horizontal; MPN GS019-2.54-04P-5

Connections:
5V: CN2.1, CN3.1, CN4.1, CN6.7, CN12.7; also elsewhere on the board
/STEP_EN: CN1.1, CN5.1; also elsewhere on the board
/VIN_12V: CN6.1, CN12.1; also elsewhere on the board
/X_DIR: CN1.8, CN5.8
/X_STEP: CN1.7, CN5.7
GND: CN2.3, CN3.3, CN4.3, CN6.8, CN12.8; also elsewhere on the board
unnamed: CN1.2, CN2.2, CN5.2
unnamed: CN1.3, CN3.2, CN5.3
unnamed: CN1.4, CN4.2, CN5.4
unnamed: CN1.5, CN5.5
unnamed: CN1.6, CN5.6
unnamed: CN6.2, CN12.2
unnamed: CN6.3, CN12.3, J12.4, J17.4
unnamed: CN6.4, CN12.4, J12.3, J17.3
unnamed: CN6.5, CN12.5, J12.2, J17.2
unnamed: CN6.6, CN12.6, J12.1, J17.1

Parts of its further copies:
CN7, CN8, CN9: CFG1; H3-2.54
CN10, CN13: FEMALE_LEFT; H8-2.54; MPN F185-1108A1BSYC1
CN11, CN14: FEMALE_RIGHT; H8-2.54; MPN F185-1108A1BSYC1
J14: MotorHeader; H4-2.54; MPN P125-1104A0BS116A1
J18: MotorHeader; TerminalBlock_Phoenix_MPT-0,5-4-2.54_1x04_P2.54mm_Horizontal; MPN GS019-2.54-04P-5

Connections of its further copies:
5V: CN7.1, CN8.1, CN9.1, CN11.7, CN14.7; also elsewhere on the board
/STEP_EN: CN10.1, CN13.1; also elsewhere on the board
/VIN_12V: CN11.1, CN14.1; also elsewhere on the board
/Y_DIR: CN10.8, CN13.8
/Y_STEP: CN10.7, CN13.7
GND: CN7.3, CN8.3, CN9.3, CN11.8, CN14.8; also elsewhere on the board
unnamed: CN7.2, CN10.2, CN13.2
unnamed: CN8.2, CN10.3, CN13.3
unnamed: CN9.2, CN10.4, CN13.4
unnamed: CN10.5, CN13.5
unnamed: CN10.6, CN13.6
unnamed: CN11.2, CN14.2
unnamed: CN11.3, CN14.3, J14.4, J18.4
unnamed: CN11.4, CN14.4, J14.3, J18.3
unnamed: CN11.5, CN14.5, J14.2, J18.2
unnamed: CN11.6, CN14.6, J14.1, J18.1

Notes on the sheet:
!Enable
CFG1
CFG2
CFG3
!Reset
!Sleep
Step
Dir
VMot
Gnd
MotB-
MotB+
MotA-
MotA+
Vdd

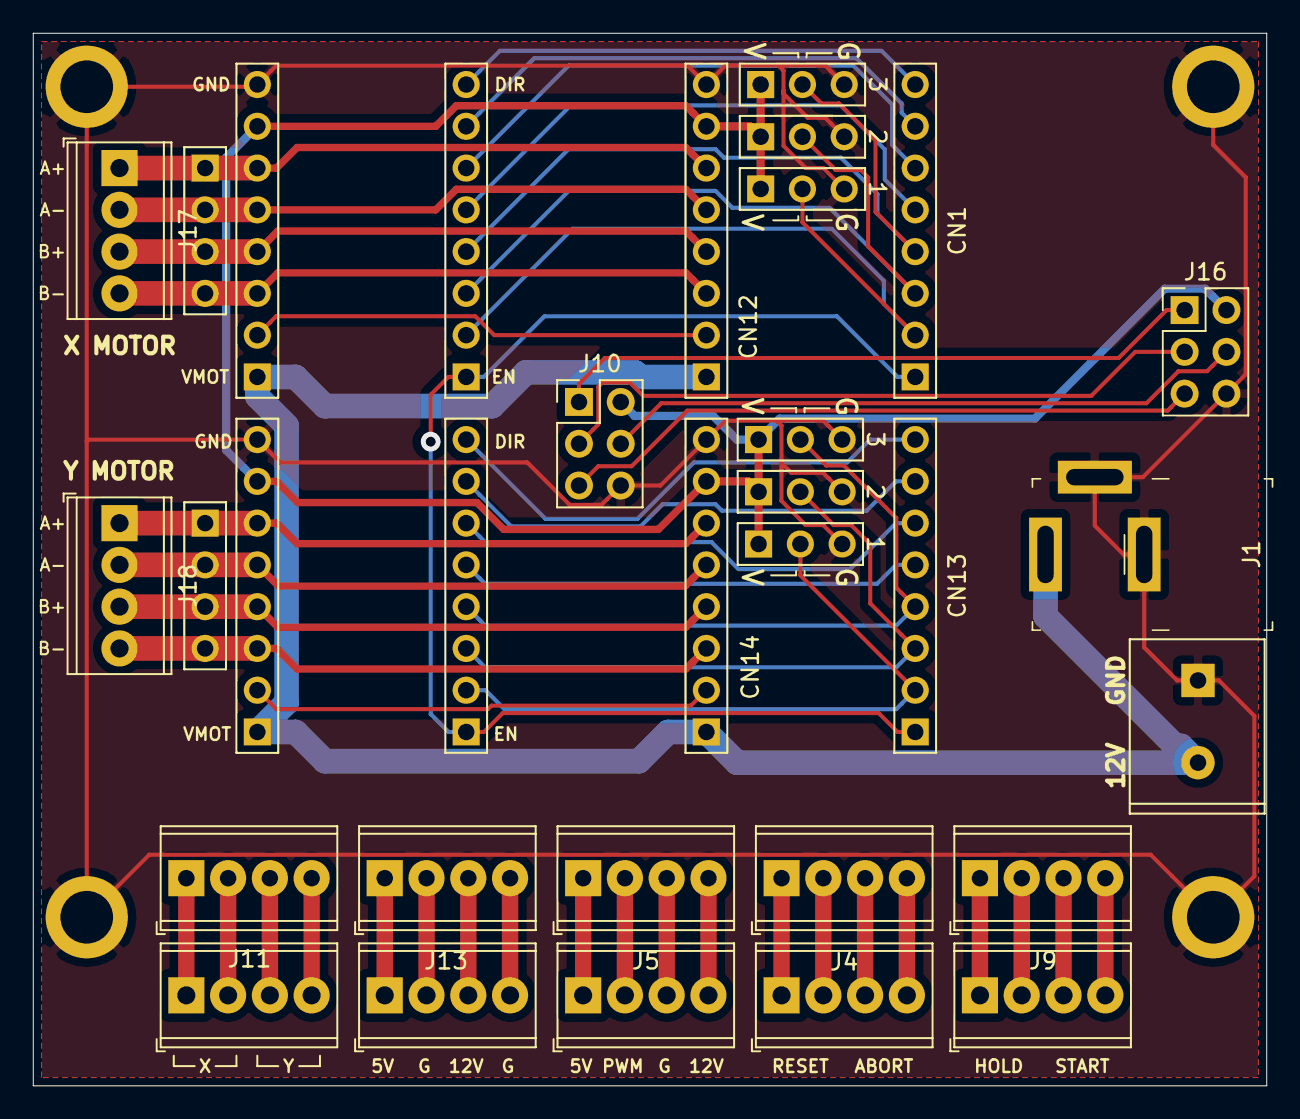
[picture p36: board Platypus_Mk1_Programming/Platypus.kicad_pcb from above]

Board: 2 copper layers, 75.0 x 64.0 mm, 36 parts (0 on the bottom side), 52 nets.

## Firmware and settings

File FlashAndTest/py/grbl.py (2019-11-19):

from . com import Serial

ERROR_MSG = {
    1: "G-code words consist of a letter and a value. Letter was not found.",
    2: "Numeric value format is not valid or missing an expected value.",
    3: "Grbl '$' system command was not recognized or supported.",
    4: "Negative value received for an expected positive value.",
    5: "Homing cycle is not enabled via settings.",
    6: "Minimum step pulse time must be greater than 3usec",
    7: "EEPROM read failed. Reset and restored to default values.",
    8: "Grbl '$' command cannot be used unless Grbl is IDLE. Ensures smooth operation during a job.",
    9: "G-code locked out during alarm or jog state",
    10: "Soft limits cannot be enabled without homing also enabled.",
    11: "Max characters per line exceeded. Line was not processed and executed.",
    12: "(Compile Option) Grbl '$' setting value exceeds the maximum step rate supported.",
    13: "Safety door detected as opened and door state initiated.",
    14: "(Grbl-Mega Only) Build info or startup line exceeded EEPROM line length limit.",
    15: "Jog target exceeds machine travel. Command ignored.",
    16: "Jog command with no '=' or contains prohibited g-code.",
    17: "Laser mode requires PWM output.",
    20: "Unsupported or invalid g-code command found in block.",
    21: "More than one g-code command from same modal group found in block.",
    22: "Feed rate has not yet been set or is undefined.",
    23: "G-code command in block requires an integer value.",
    24: "Two G-code commands that both require the use of the XYZ axis words were detected in the block.",
    25: "A G-code word was repeated in the block.",
    26: "A G-code command implicitly or explicitly requires XYZ axis words in the block, but none were detected.",
    27: "N line number value is not within the valid range of 1 - 9,999,999.",
    28: "A G-code command was sent, but is missing some required P or L value words in the line.",
    29: "Grbl supports six work coordinate systems G54-G59. G59.1, G59.2, and G59.3 are not supported.",
    30: "The G53 G-code command requires either a G0 seek or G1 feed motion mode to be active. A different motion was active.",
    31: "There are unused axis words in the block and G80 motion mode cancel is active.",
    32: "A G2 or G3 arc was commanded but there are no XYZ axis words in the selected plane to trace the arc.",
    33: "The motion command has an invalid target. G2, G3, and G38.2 generates this error, if the arc is impossible to generate or if the probe target is the current position.",
    34: "A G2 or G3 arc, traced with the radius definition, had a mathematical error when computing the arc geometry. Try either breaking up the arc into semi-circles or quadrants, or redefine them with the arc offset definition.",
    35: "A G2 or G3 arc, traced with the offset definition, is missing the IJK offset word in the selected plane to trace the arc.",
    36: "There are unused, leftover G-code words that aren't used by any command in the block.",
    37: "The G43.1 dynamic tool length offset command cannot apply an offset to an axis other than its configured axis. The Grbl default axis is the Z-axis.",
    38: "Tool number greater than max supported value.",
}

class grbl(Serial):
    def __init__(self, hardwareID="1A86:7523"):
        super().__init__(hardwareID=hardwareID)

        self.startup()

    def startup(self):
        if not self.connected:
            self.dev = None
            self.connect()
        if self.connected:
            # read and clear connection header
            # Grbl 1.1f ['$' for help]
            self.get_response()

    def get_response(self):
        lines = []
        result = False
        while True:
            l = self.readline()
            if l is None:
                return False, []
            l = l.strip()
            print('> {}'.format(l))
            if l.startswith('Grbl'):
                # startup output, ignore
                result = True
                break  # no more needed
            elif l.startswith('ok'):
                result = True
                break
            elif l.startswith('error'):
                result = False
                _, code = l.split(':')
                code = int(code)
                if code in ERROR_MSG:
                    print('\nERROR: {}\n'.format(ERROR_MSG[code]))
                break
            else:
                lines.append(l)

        return result, lines

    def send(self, cmd):
        print('>> {}'.format(cmd))
        self.write(cmd)
        r, l = self.get_response()
        if not r:
            print('Error running {}, see console'.format(cmd))
        return l

    def get_config(self):
        lines = self.send('$$')
        cfg = {}
        for l in lines:
            if not l.startswith('$'):
                continue
            print(l)
            k, v = l.split('=')
            cfg[k] = float(v)
        return cfg

    def get_pos(self):
        status = self.send('?')[0]
        pos = status.split('|')[1]
        return [float(v) for v in pos.split(':')[1].split(',')]

    def home(self):
        self.send('$H')
        return self.get_pos()

    def unlock(self):
        self.send('$X')

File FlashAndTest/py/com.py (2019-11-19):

import sys
import time
import os
import traceback

import serial
import serial.tools.list_ports

class Serial(object):
    def __init__(self, dev="", hardwareID=None, baud=115200):

        self._hardwareID = hardwareID
        self.baud = baud
        self._com = None
        self.dev = dev
        self.connected = False

        self.connect()

    def __exit__(self, type, value, traceback):
        if self._com is not None:
            print("Closing connection to: %s", self.dev)
            self._com.close()

    def findSerialDevices(self, hardwareID):
        hardwareID = "(?i)" + hardwareID  # forces case insensitive
        foundDevices = []
        for port in serial.tools.list_ports.grep(hardwareID):
            foundDevices.append(port[0])

        return foundDevices

    def connect(self):
        self.connected = self._connect()
        return self.connected

    def _connect(self):
        try:
            if(self.dev == "" or self.dev is None):
                try:
                    self.dev = self.findSerialDevices(self._hardwareID)[0]
                except IndexError:
                    return False

            print("Using COM Port: {}".format(self.dev))

            self._com = serial.Serial(self.dev, baudrate=self.baud, timeout=5)

            return True

        except serial.SerialException as e:
            error = "Unable to connect to the device. Please check that it is connected and the correct port is selected."
            print(traceback.format_exc())
            print(error)
            raise e

    def write(self, data, nl=True):
        try:
            if nl and not data.endswith('\n'):
                data += '\n'
            self._com.write(data.encode('utf-8'))
        except serial.serialutil.SerialException:
            self.connected = False

    def readline(self):
        try:
            resp = self._com.readline()
            return resp.decode()
        except serial.serialutil.SerialException:
            self.connected = False

class Encoder(Serial):
    def __init__(self):
        # super().__init__(hardwareID="16C0:0483")
        super().__init__(dev='/dev/ttyACM0')

        self.read()  # read once to reset state

    def read(self):
        self.write('c', False)
        resp = self.readline().strip()
        try:
            deltas = resp.split(',')
            return (int(deltas[0]), int(deltas[1]))
        except:
            print('Error reading encoder values')
            return (0,0)

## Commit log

2019-08-06 initial setup
    [Controller.kicad_pcb, Controller.sch]
2019-08-06 Added Arduino Nano component
    [nano.sch]
2019-08-06 Add nano to main sheet
    [Controller.sch, nano.sch]
2019-08-06 Starting on step driver module
    [Controller.sch, nano.sch, step_driver.sch]
2019-08-07 Minor update to stepper
    [step_driver.sch]
2019-08-07 Almost complete schematic
    [Controller.sch, nano.sch, step_driver.sch]
2019-08-07 Complete schematic
    [Controller.sch, nano.sch, step_driver.sch]
2019-08-07 Set more footprints
    [Controller.sch, nano.sch, step_driver.sch]
2019-08-07 Add IC footprints
    [nano.sch, step_driver.sch]
2019-08-08 Creating Pi layout
    [Controller.sch, nano.sch, step_driver.sch]
2019-08-08 Probably giving up on Pi option
    [Controller.kicad_pcb, nano.sch, step_driver.sch]
2019-08-09 More power routing
    [Controller.csv, Controller.kicad_pcb, Controller.sch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]
2019-08-09 power and nano cleanup
    [Controller.kicad_pcb, nano.sch, step_driver.sch]
2019-08-10 Mostly final layout
    [Controller.kicad_pcb, Controller.sch, nano.sch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]
2019-08-10 Near complete layout
    [Controller.kicad_pcb]
2019-08-10 Beta v1
    [Controller-B_Cu.gbr, Controller-B_Fab.gbr, Controller-B_Mask.gbr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]
2019-08-10 Starting to add 3D models
    [Controller.kicad_pcb]
2019-08-10 Finished adding 3D models
    [Controller.kicad_pcb, Controller.sch, step_driver.sch]
2019-08-10 Fixing 10uF caps
    [Controller.kicad_pcb, Controller.sch, nano.sch]
2019-08-10 fix 2 missing cap models
    [Controller.kicad_pcb]
2019-08-14 Add fab files
    [BOM.csv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]
2019-08-29 Moving into own repo
    [BOM.csv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]
2019-08-30 Increase mount hole size
    [Platypus.kicad_pcb]
2019-09-09 Change RX/TX LEDs. Add new laser conn
    [Platypus.kicad_pcb, Platypus.sch, nano.sch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]
2019-09-09 rework for component moves
    [Platypus.kicad_pcb, Platypus.sch, nano.sch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]
2019-09-10 Adding platypus graphic
    [Platypus.kicad_pcb]
2019-09-11 Update fab files
    [BOM.csv, BOM_with_TH_Parts.csv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]
2019-09-11 Addinge license note to board back
    [Platypus.kicad_pcb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]
2019-09-11 Adding stepper driver labels
    [Platypus.kicad_pcb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]
2019-10-09 Adding step file and solder jig
    [SolderJig.stl]
2019-10-11 remove boarder from gerbers
    [Platypus-B_SilkS.gbr, Platypus-Edge_Cuts.gbr, Platypus-F_SilkS.gbr]
2019-10-17 Add programming board
    [BOM.csv, BOM_with_TH_OPL_Parts.csv, BOM_with_TH_Parts.csv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]
2019-11-05 Fixing programmer hole sizes
    [Platypus.kicad_pcb]
2019-11-11 add laserweb doc
2019-11-11 Added driver section
2019-12-15 Adding assembly guide
2019-12-15 Add assembly link
2019-12-15 Adding dimensions doc
    [Platypus.kicad_pcb]
2019-12-16 tweak assembly guide

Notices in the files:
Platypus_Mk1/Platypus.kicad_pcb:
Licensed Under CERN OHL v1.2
